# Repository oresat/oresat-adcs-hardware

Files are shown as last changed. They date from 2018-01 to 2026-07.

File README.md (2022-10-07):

# oresat-adcs-hardware

For more information on the OreSat project, please see <https://www.oresat.org/>!

## About this Repo

This repo contains the following projects:

* **The OreSat ADCS Card**
   * ADCS M0 microcontroller on its own OreSat Power Domain (OPD)
      * Power switch and LTC4300 that connects the M0 to:
         * BMI088 IMU (onboard the ADCS card)
         * LTC4305 2-Channel I2C Bus Multiplexer (one on each end cap via the backplane, end cards, and connectors to the end caps)
            * Two MMC5883MA magnetometers (two on each end cap, multiplexed by the LTC4305s)
      * Three STSPIN250s for the X, Y, and Z magnetorquers
   * Q1 Reaction Wheel OPD which powers the Q1 RW board
   * Q2 Reaction Wheel OPD which powers the Q2 RW board
   * Q3 Reaction Wheel OPD which powers the Q3 RW board
   * Q4 Reaction Wheel OPD which powers the Q4 RW board
* **OreSat RW boards**
   * Boards that run one of the four reaction wheels that we have.
   * Note that the "flat" version of the boards are for development

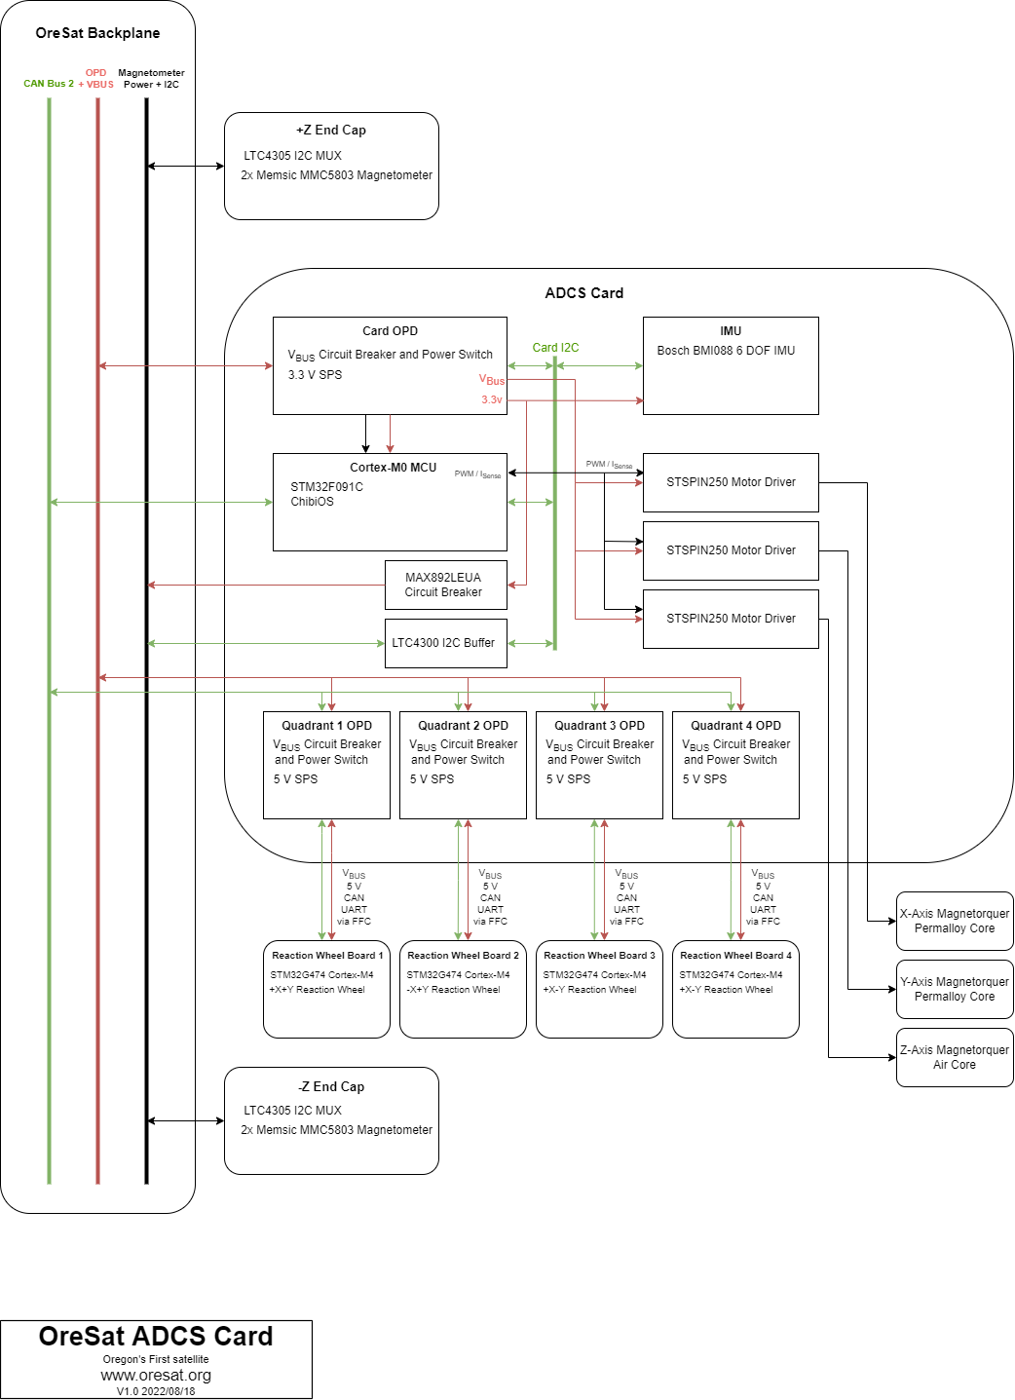
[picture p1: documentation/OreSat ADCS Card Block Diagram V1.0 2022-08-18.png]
ADCS Card Block Diagram


## LICENSE

Copyright the Portland State Aerospace Society, 2022.

This source describes Open Hardware that is licensed under CERN-OHL-S v2, or any later version.

You may redistribute and modify this source and make products using it under the terms of the CERN-OHL-S v2 (https://ohwr.org/cern_ohl_s_v2.txt).

This source is distributed WITHOUT ANY EXPRESS OR IMPLIED WARRANTY, INCLUDING OF MERCHANTABILITY, SATISFACTORY QUALITY AND FITNESS FOR A PARTICULAR PURPOSE. Please see the CERN-OHL-S v2 for applicable conditions.

Source location: https://github.com/oresat/

As per CERN-OHL-S v2 section 4, should You produce hardware based on this source, You must where practicable maintain the Source Location visible on the external case of the Gizmo or other products you make using this source.

# DEPRECATED - PLEASE EVENTUALLY REWRITE :)

## The OreSat Project
OreSat is an inter university collaboration to design an orbital vehicle. Once in orbit, the nanosatellite will engage in three missions. One of the missions is space testing a relatively new photovoltaic panel. The other missions require the ability to point at and maintain visual contact with a specified location. 
## Background Motivation   
In order to successfully complete these missions, OreSat will need to be able to articulate its orientation as well as its passive “drifting” spin (we’ll discuss what “passive spin” means a little later). 
Quick and reliable orientation adjustment and control will serve several purposes. It will allow the vehicle to direct its main camera, as well as giving it the ability to execute maneuvers that allow it to maintain visual and radio contact with a specific location. This makes taking photos and videos much easier, but it also allows us to have a segment of time to do large bandwidth data dumps to ground stations. This gives it the potential to do live video streaming. 
### Active Pointing
The method that was selected for active orientation on OreSat employs the use of internal spinning masses called reaction wheels. The basic principle is simple. If there is a free floating object and a section of it starts to spin, the rest of the body will react by spinning in the opposite direction. The spin rates are related, but not necessarily the same. If you’d like to look more into this, the concept is conservation of angular momentum. 
So the idea is that we have a pointing vector for Oresat (not poynting, that comes later), and an idea of the pointing vector to the location we would like to image. We simply take the difference, and then rotate the collective mass of all of the reaction wheels in the opposite direction until the satellite camera sees what we want it too.  
### Passive Spin Control
The term “passive spin” will be used to refer the net angular momentum of the nanosatellite. While the reaction wheels are active, they are able to control the direction and spin of the frame of the satellite, but only by effectively redistributing the momentum from the frame into the reaction wheel masses. The reaction wheels are incapable of altering the net angular momentum. The need for being able to modify the net momentum vector of the satellite helps alleviate the burden of two issues. The issues are thermal regulation and power generation. OreSat only has photovoltaic panels of its elongated faces. To maximize the amount of power, the desired passive spin of the satellite would put the long axis perpendicular to the sun. This maximizes the surface of exposure. There is another part to the total momentum though, and that is its magnitude. The rate of spin effects several things, but most notably it affects the temperature gradient experience by OreSat. If the satellite has no spin, then the side that the sun is hitting will heat continuously until OreSat passes behind the earth. This can cause several issues, most simply that having a hot spot would increase the likelihood of an electrical system to failing. Another issue is that the hot spot will cause different amounts of expansion in different areas of the frame, increasing the likelihood of failure. Another issue that hot spots cause is a drop in efficiency of the solar panels, making rotation partially an energy problem as well. 
Adding an intentional spin to OreSat will even out the thermal load applied to 

The attitude control system (ACS) inside oresat needs to orientate the position of the cubesat in space. This will be acheived in two ways; With brushless DC motors (BLDC) and with Magnetorquers. We are designing a PCB that controls both systems.

Find the project design contraints at,
[Project Design Constraints](https://github.com/oresat/oresat-acs-board/blob/master/Project%20Design%20Constraints.md)

ACS Level 2 Block Diagram Version 3.2
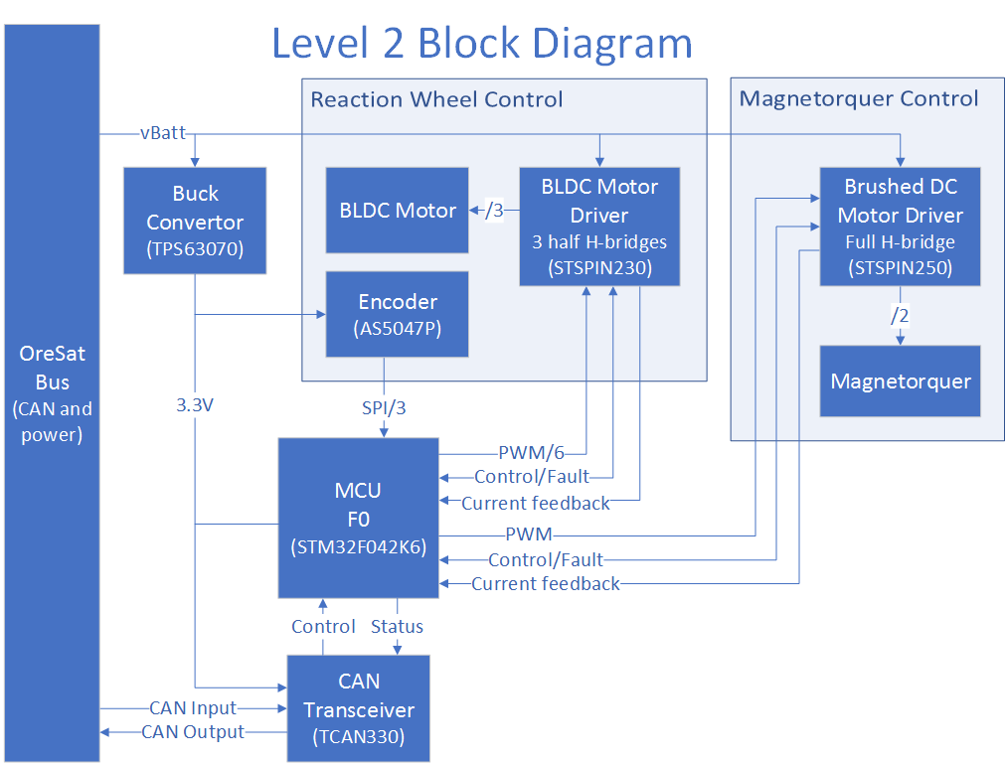
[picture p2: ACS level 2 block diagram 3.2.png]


### System Hardware Overview
[Deatailed Hardware Reference Guide](https://github.com/oresat/oresat-acs-board/tree/master/Component%20File)

### EagleCAD Files:
[Link to the EagleCAD schematics and board layouts](https://github.com/oresat/oresat-acs-board/tree/master/eaglecad)

### Manufacturing Photos:
[Manufacturing photos of board layouts and CAD model of mounting strategy](https://github.com/oresat/oresat-acs-board/tree/master/Manufacturing%20photos)

### Capstone Poster:
[Link to Capstone poster in Google Drive](https://docs.google.com/presentation/d/1KBfbX376Y7nvsIXe14JdyOgP9TMmgJlgeOiYP8BOekc/edit#slide=id.p1)
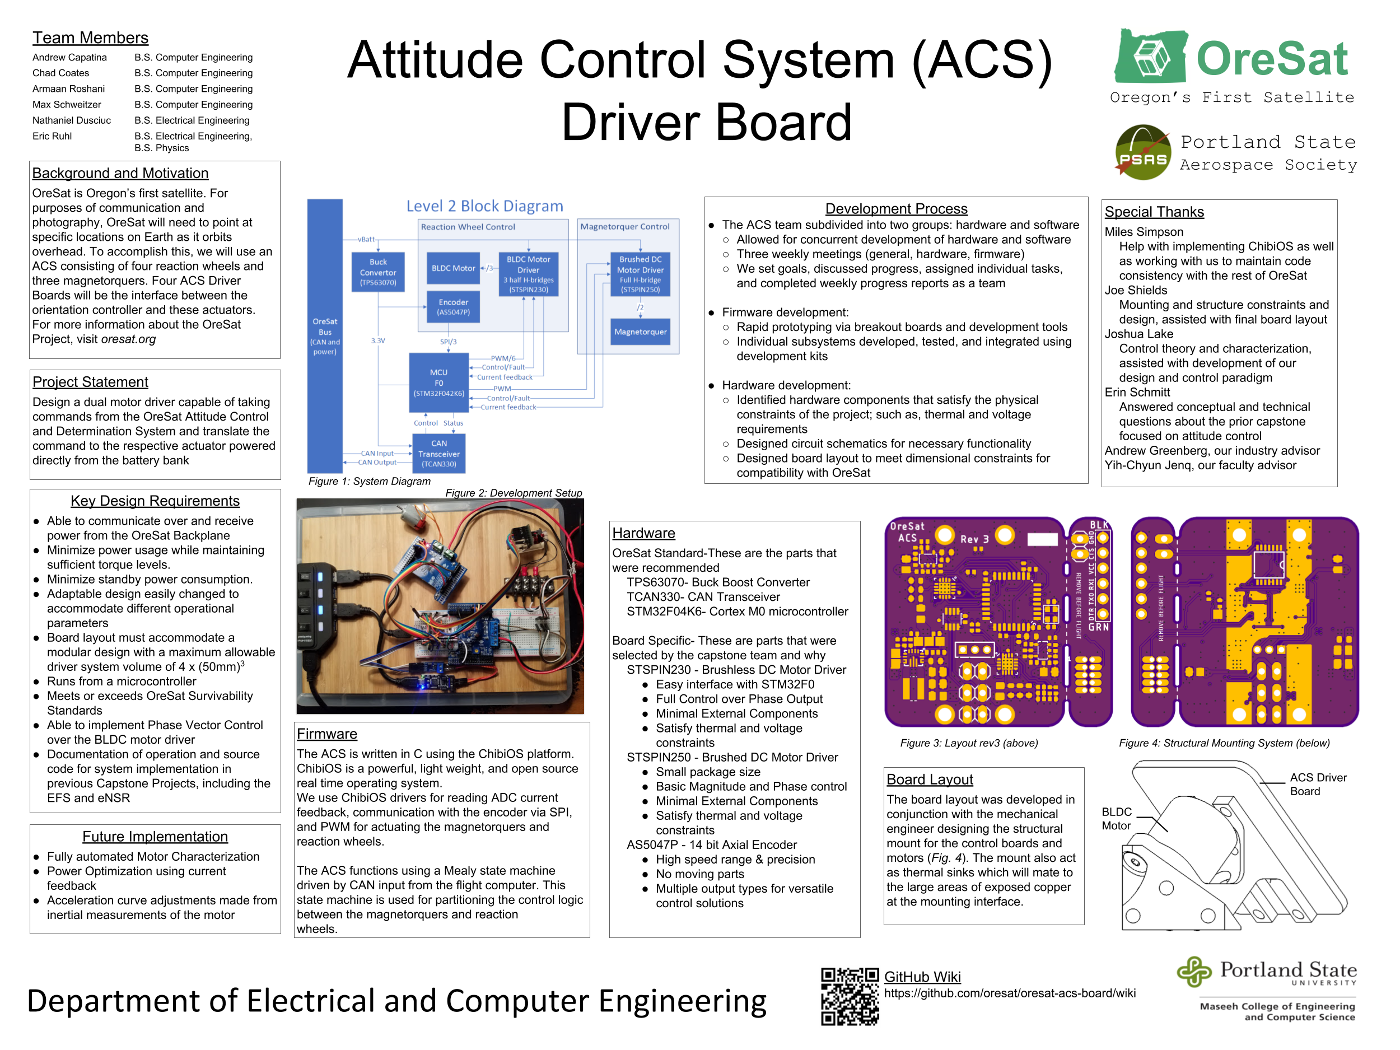
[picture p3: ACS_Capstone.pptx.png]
Image of Capstone poster


### System Firmware:
[Check here for the firmware information](https://github.com/oresat/oresat-firmware/wiki/ACS-Firmware)

### Research and Tutorials / Ramp Up Documents:
Brushless DC (BLDC) motor control is a challenging form of motor control. We found numerous helpful tutorials and references.
[Link to research references and bibliography, start here for a ramp up on ACS](https://github.com/oresat/oresat-acs-board/blob/master/Ramp%20Up.md)

## Final Product:
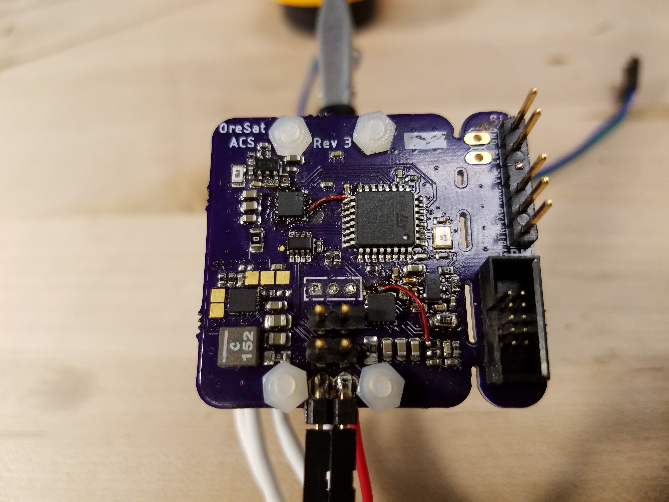
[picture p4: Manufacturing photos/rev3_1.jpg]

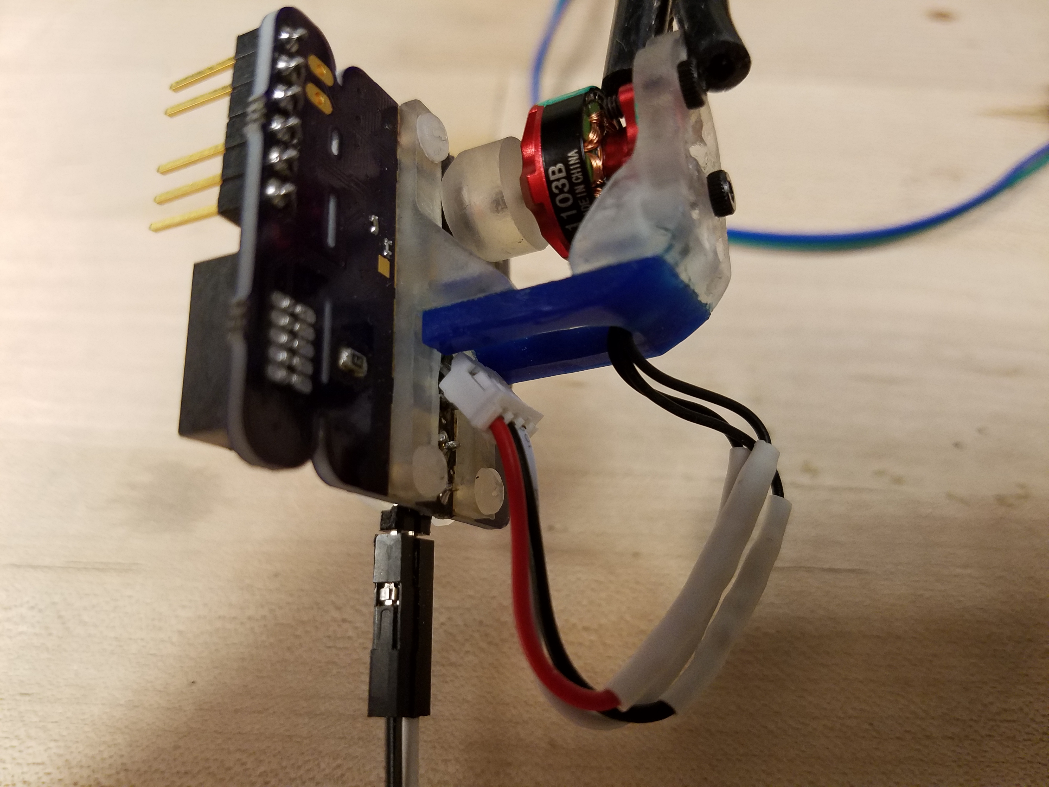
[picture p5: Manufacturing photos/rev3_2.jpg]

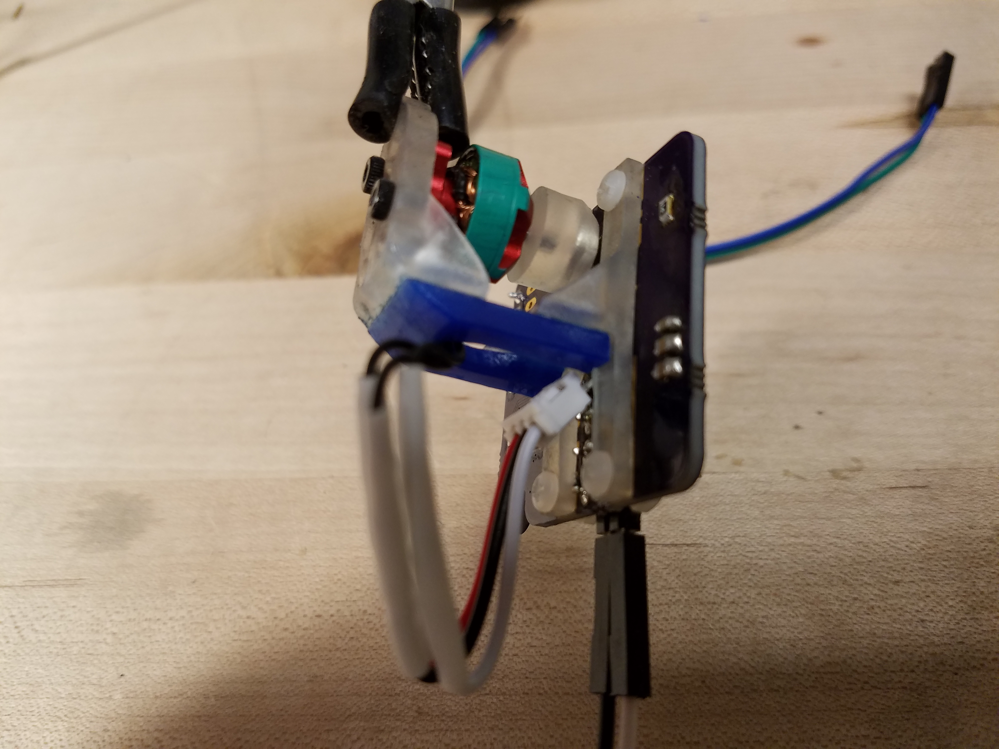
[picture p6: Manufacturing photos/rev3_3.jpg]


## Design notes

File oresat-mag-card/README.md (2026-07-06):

---
title: "**OreSat Mag Card**"
subtitle: |
  **Fabrication and Assembly Information**\
  For build TIME-STAMP
fontsize: 10pt
geometry:
  - margin=0.5in
toc: true
toc-depth: 2
colorlinks: true
urlcolor: blue
---

\newpage

# About this Board

## Board Description

The OreSat Mag Card handles three things for the open source [OreSat CubeSat system](https://www.oresat.org/):

- Reads the four magnetometers located on the end caps of the satellite and broadcasts the data on the CAN bus.
- Reads the 6 DOF inertial measurement unit (IMU) and broadcasts the data on the CAN bus (mostly just the gyroscopes).
- Runs the three magnetorquers based on commands from the C3 via the CAN bus.

## Documentation Links

- Mag card hardware Git repository: <https://github.com/oresat/oresat-adcs-hardware>
- **TODO:** Mag card Design Notes + Design Review Notes

## Documentation Files

| Filename | Notes |
| --- | --- |
| README.pdf | This README file |
| PROJECT-NAME-outline.dxf | Board outline (with holes) in DXF format |
| PROJECT-NAME-pcba.step | 3D model of PCBA (with components) |
| PROJECT-NAME-render-bot.jpg | Render of the top of the 3D model |
| PROJECT-NAME-render-bot.jpg | Render of the bottom of the 3D model |
| PROJECT-NAME-schematic.pdf | PDF of board schematics |

## Contact Information

- Website: <https://www.oresat.org/>
- Email: <oresat@pdx.edu>
- Instagram: @pdxaerospace

## Board Renders

Render of the top of the 3D model
Render of the bottom of the 3D model

\newpage

# Printed Circuit Board (PCB) Fabrication Information

## Board Info

- 4 layer board
- Bounding box is 99.8 x 94.6 mm (3.93 x 3.72 in)
- Board thickness is 1.59 mm (0.063 inch)

## Board Requirements

- Design Rules
    - Minimum Trace / Space design rules
       - Outer layers: 0.127 mm (5.0 mil) / 0.127 mm (5.0 mil)
       - Inner layers: 0.127 mm (5.0 mil) / 0.127 mm (5.0 mil)
    - Outer dimension router tolerance: +/- 0.254 mm (10.0 mil)
    - Hole placement tolerance: +/- 0.075 mm (3.0 mil)
    - Inner tab routed slot tolerance: +/- 0.254 mm (10.0 mil)
- Drills
   - Drill Positional Tolerance: 0.051 mm (2.0 mil)
   - Drill Size tolerance: +/- 0.064 mm (2.5 mil)
- Plated/Un-plated holes
  - There are 8 un-plated (NPT) holes
  - There are 730 plated through (PTH) holes
  - PTH minimum diameter: 0.254 mm (10 mil)
  - PTH minimum annulus: 0.102 mm (4 mil) radius
- Outline/Routing
  - Requires a 1.0 mm or smaller diameter routing bit
- Slots/Cutouts
  - There is one cutout.
- There are 3 fiducials on the top layer.
- Panel tabs ("mouse bites")
   - Card edges must be smooth; no mouse bites or other intrusions into the card outline.
   - If external mouse bites are required, minimize and customer will remove by hand before assembly.
- If not otherwise specified, build to IPC 6012 Class 2 or better.

## Materials

- No controlled impedance.
- Outer layers must be 1 oz Copper, inner layers can be 0.5 or 1.0 oz Copper.
- Isola FR408HR or material recommended.
- Board Surface treatment should be ENIG, althogh immersion Silver is acceptable.
- White silkscreen on top and bottom surface
- Taiyo PSR-4000 or equivalent soldermask on top and bottom, no requirements for color.

## Suggested Stack Up

| Layer | Thickness | Notes |
|---|---|---|
| Top Copper | 0.043 mm /  1.7 mil |  Layer 1 foil, 1 oz Cu after plating |
| prepreg | 0.200 mm /  7.9 mil |  Prepreg - Isola FR408HR 2113 |
| Layer 2 | 0.018 mm /  0.7 mil |  Layer 2 foil, 0.5 oz Cu |
| Core | 0.991 mm / 39 mil |  Core Isola FR408HR |
| Layer 3 | 0.018 mm /  0.7 mil |  Layer 3 foil, 0.5 oz Cu |
| prepreg | 0.200 mm /  7.9 mil |  Prepreg - Isola FR408HR 2113 |
| Bottom Copper | 0.043 mm /  1.7 mil |  Layer 4 foil, 1 oz copper after plating |
| **Total Stackup** | **1.588 mm / 62.5 mil** | |

## Array / Panel Information

- Coordinate with Contract Manufacturer (CM) for optimal size of this panel.
- If no feedback from CM, then produce single boards (no panel).

## Fabrication Files

### IPC-2581 File

| Filename | Notes |
| --- | --- |
| PROJECT-NAME-ipc2581.xml | IPC-2581 board information file |

### Legacy PCB Files

| Filename | Notes |
| ---| --- |
| PROJECT-NAME-Edge_Cuts.gbr | RS274X file for the dimension (outline) layer |
| PROJECT-NAME-F_Silkscreen.gbr | RS274X file for the top silkscreen |
| PROJECT-NAME-F_Mask.gbr | RS274X file for the top soldermask |
| PROJECT-NAME-F_Cu.gbr | RS274X file for the top copper layer |
| PROJECT-NAME-In1_Cu.gbr | RS274X file for the layer 2 copper |
| PROJECT-NAME-In2_Cu.gbr | RS274X file for the layer 3 copper |
| PROJECT-NAME-B_Cu.gbr | RS274X file for the bottom copper layer |
| PROJECT-NAME-B_Mask.gbr | RS274X file for the bottom soldermask |
| PROJECT-NAME-B_Silkscreen.gbr | RS274X file for the bottom silkscreen |
| PROJECT-NAME-NPTH.drl | Excellon file for non-plated through holes |
| PROJECT-NAME-PTH.drl | Excellon file for plated through holes | 

\newpage

# Printed Circuit Board Assembly (PCBA) Information

## Assembly Info

- This PCBA is surface mount (SMT) components with 4 through-hole (TH) components.
- Components are only on the top side of the board.

## Assembly Requirements

- Assemble to IPC Class 2 or better
- Bake components that are not moisture sealed to appropriate levels as required.
- Solder paste MUST be leaded.
- Aqueous flux and wash strongly preferred.
   - Clean to NASA Standard "Visibly Clean (VC)": No particles or residues are visible to the naked eye.
- No conformal coating.
- Ship in antistatic protective bag

## Component Specific Assembly Information

- No specific requirements.

## Assembly Files

### IPC-2581 File

| Filename | Notes |
| --- | --- |
| PROJECT-NAME-ipc2581.xml | IPC-2581 board information file |

### Bill of Materials (BOM)

| Filename | Description |
| --- | --- |
| PROJECT-NAME-bom.csv | BOM in Comma Separated Variable format |

### Solder Paste Stencils

| Filename | Notes |
| --- | --- |
| PROJECT-NAME-B_Paste.gbr | RS274X file for top/front solder paste stencil |
| PROJECT-NAME-F_Paste.gbr | RS274X file for bottom/back solder paste stencil |

### Mounting/Placement Location

| Filename | Description |
| --- | --- |
| PROJECT-NAME-3u.pos | Pick and place locations for components |

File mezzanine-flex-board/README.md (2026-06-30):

---
title: "**OreSat Reaction Wheel Flex Board**"
subtitle: |
  **Fabrication and Assembly Information**\
  For build TIME-STAMP
fontsize: 10pt
geometry:
  - margin=0.5in
toc: true
toc-depth: 2
colorlinks: true
urlcolor: blue
---

\newpage

# About this Board

## Board Description

This flexible circuit board connects the OreSat Reaction Wheel boards (the boards that control each reaction wheel) to the
the OreSat RW Card, which handles the OreSat Power Domain for each RW. For more information, see the open source 
[OreSat CubeSat system](https://www.oresat.org/)

## Documentation Links

- Git repository: <https://github.com/oresat/oresat-adcs-hardware>
- **TODO:** Link to Design Notes + Design Review Notes

## Documentation Files

| Filename | Notes |
| --- | --- |
| README.pdf | This README file |
| PROJECT-NAME-outline.dxf | Board outline (with holes) in DXF format |
| PROJECT-NAME-pcba.step | 3D model of PCBA (with components) |
| PROJECT-NAME-render-bot.jpg | Render of the top of the 3D model |
| PROJECT-NAME-render-bot.jpg | Render of the bottom of the 3D model |
| PROJECT-NAME-schematic.pdf | PDF of board schematics |

## Contact Information

- Website: <https://www.oresat.org/>
- Email: <oresat@pdx.edu>
- Instagram: @pdxaerospace

## Board Renders

Render of the top of the 3D model
Render of the bottom of the 3D model

Note that renders do not show stiffeners.

\newpage

# Printed Circuit Board (PCB) Fabrication Information

## Board Info

- 2 layer board
- Bounding box is 39.5 x 10.2 mm
- Flexible PCB with two polimide stiffeners (see below)
- Note that these boards were originally run and tested using JLCPCB's flexible PCB service.

## Board Requirements

- Design Rules
    - Minimum Trace / Space design rules
       - Outer layers: 0.127 mm (5.0 mil) / 0.127 mm (5.0 mil)
       - Inner layers: 0.127 mm (5.0 mil) / 0.127 mm (5.0 mil)
    - Outer dimension router tolerance: +/- 0.254 mm (10.0 mil)
    - Hole placement tolerance: +/- 0.075 mm (3.0 mil)
    - Inner tab routed slot tolerance: +/- 0.254 mm (10.0 mil)
- Drills
   - Drill Positional Tolerance: 0.051 mm (2.0 mil)
   - Drill Size tolerance: +/- 0.064 mm (2.5 mil)
- Plated/Un-plated holes
  - PTH minimum diameter: 0.3 mm (11.8 mil)
  - PTH minimum annulus: 0.2 mm (7.9 mil)
- Outline/Routing
  - No requirements
- Slots
  - There are no slots.
- Cutouts
  - There are no cutouts.
- There are no fiducials.
- Panel tabs ("mouse bites")
   - No requirements; prefer that board edges are smooth; no mouse bites or other intrusions into the card outline.
   - If external mouse bites are required, minimize and customer will remove by hand before assembly.
- If not otherwise specified, build to IPC 6012 Class 2 or better.

## Materials

- No controlled impedance.
- Note that these boards were originally run and tested using JLCPCB's flexible PCB service, and so numbers here are arbitrarily from that service. Other thicknesses can be used, contact us to discuss.
- 0.33 to 0.5 oz Copper.
- Polyimide flexible circuit material, 25 um thick dielectric
- Coverlay (soldermask equivalent) is 12.5 um Polyimide
- There are two 0.25 mm thick Polyimide stiffeners on the TOP surface, one on each end.
   - These can be FR4 stiffeners if easier / cheaper. 
- Board Surface treatment should be ENIG.
- White silkscreen on top and bottom surface

## Suggested Stack Up

| Layer | Thickness | Notes |
|---|---|---|
| Top Stiffener | 0.25 mm  / 9.84 mils | Stiffener on top surface of board only |
| Top Coverlay | 12.5 um /  0.49 mils | Coverlay / Solder mask |
| Top Copper | 18.0 um /  0.71 mils | Layer 1 foil, 0.5 oz Cu after plating  |
| Polyimide Core  | 25.0 um /  0.98 mils | Polyimide flex material |
| Bottom Copper | 18.0 um /  0.71 mils | Layer 2 foil, 0.5 oz Cu after plating  |
| Bottom Coverlay | 12.5 um /  0.49 mils | Coverlay / Solder mask |

Total thickness: 86 um (without stiffener)

## Array / Panel Information

- No panel or array required.

## Fabrication Files

### IPC-2581 File

| Filename | Notes |
| --- | --- |
| PROJECT-NAME-ipc2581.xml | IPC-2581 board information file |

### Legacy PCB Files

| Filename | Notes |
| --- | --- |
| PROJECT-NAME-Edge_Cuts.gbr | RS274X file for the dimension (outline) layer |
| PROJECT-NAME-F_Silkscreen.gbr | RS274X file for the top silkscreen |
| PROJECT-NAME-F_Mask.gbr | RS274X file for the top soldermask |
| PROJECT-NAME-F_Cu.gbr | RS274X file for the top copper layer |
| PROJECT-NAME-B_Cu.gbr | RS274X file for the bottom copper layer |
| PROJECT-NAME-B_Mask.gbr | RS274X file for the bottom soldermask |
| PROJECT-NAME-B_Silkscreen.gbr | RS274X file for the bottom silkscreen |
| PROJECT-NAME-User_Stiffeners.gbr | RS274X file for PI stiffener | 
| PROJECT-NAME-PTH.drl | Excellon file for plated through holes | 

\newpage

# Printed Circuit Board Assembly (PCBA) Information

## Assembly Info

- There are SMT components only on the bottom side of the board.

## Assembly Requirements

- Assemble to IPC Class 2 or better
- Bake components that are not moisture sealed to appropriate levels as required.
- Solder paste MUST be leaded.
- Aqueous flux and wash strongly preferred.
   - Clean to NASA Standard "Visibly Clean (VC)": No particles or residues are visible to the naked eye.
- No conformal coating.

## Component Specific Assembly Information

- No specific requirements.

## Assembly Files

### IPC-2581 File

| Filename | Notes |
| --- | --- |
| PROJECT-NAME-ipc2581.xml | IPC-2581 board information file |

### Bill of Materials (BOM)

| Filename | Description |
| --- | --- |
| PROJECT-NAME-bom.csv | BOM in Comma Separated Variable format |

### Solder Paste Stencils

| Filename | Notes |
| --- | --- |
| PROJECT-NAME-B_Paste.gbr | RS274X file for top/front solder paste stencil |
| PROJECT-NAME-F_Paste.gbr | RS274X file for bottom/back solder paste stencil |

### Mounting/Placement Location

| Filename | Description |
| --- | --- |
| PROJECT-NAME-3u.pos | Pick and place locations for components |

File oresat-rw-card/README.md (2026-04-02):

---
title: "**OreSat Reaction Wheel (RW) Card**"
subtitle: |
  **Fabrication and Assembly Information**\
  For build TIME-STAMP
fontsize: 10pt
geometry:
  - margin=0.5in
toc: true
toc-depth: 2
colorlinks: true
urlcolor: blue
---

\newpage

# About this Board

## Board Description

The OreSat RW Card run the four reaction wheels on the open source [OreSat CubeSat system](https://www.oresat.org/). The RW card:

- Has an OreSat Power Domain (OPD) per reaction wheel.
- Requires a flexible cable between the card and the RW board.

## Documentation Links

- RW card hardware Git repository: <https://github.com/oresat/oresat-adcs-hardware>
- **TODO:** RW card Design Notes + Design Review Notes

## Documentation Files

| Filename | Notes |
| --- | --- |
| README.pdf | This README file |
| PROJECT-NAME-outline.dxf | Board outline (with holes) in DXF format |
| PROJECT-NAME-pcba.step | 3D model of PCBA (with components) |
| PROJECT-NAME-render-bot.jpg | Render of the top of the 3D model |
| PROJECT-NAME-render-bot.jpg | Render of the bottom of the 3D model |
| PROJECT-NAME-schematic.pdf | PDF of board schematics |

## Contact Information

- Website: <https://www.oresat.org/>
- Email: <oresat@pdx.edu>
- Instagram: @pdxaerospace

## Board Renders

Render of the top of the 3D model
Render of the bottom of the 3D model

\newpage

# Printed Circuit Board (PCB) Fabrication Information

## Board Info

- 4 layer board
- Bounding box is 99.8 x 94.6 mm (3.93 x 3.72 in)
- Board thickness is 1.59 mm (0.063 inch)

## Board Requirements

- Design Rules
    - Minimum Trace / Space design rules
       - Outer layers: 0.127 mm (5.0 mil) / 0.127 mm (5.0 mil)
       - Inner layers: 0.127 mm (5.0 mil) / 0.127 mm (5.0 mil)
    - Outer dimension router tolerance: +/- 0.254 mm (10.0 mil)
    - Hole placement tolerance: +/- 0.075 mm (3.0 mil)
    - Inner tab routed slot tolerance: +/- 0.254 mm (10.0 mil)
- Drills
   - Drill Positional Tolerance: 0.051 mm (2.0 mil)
   - Drill Size tolerance: +/- 0.064 mm (2.5 mil)
- Plated/Un-plated holes
  - There are 2 un-plated (NPT) holes
  - There are 664 plated through (PTH) holes
  - PTH minimum diameter: 0.254 mm (10 mil)
  - PTH minimum annulus: 0.102 mm (4 mil) radius
- Outline/Routing
  - Requires a 1.0 mm or smaller diameter routing bit
- Slots
  - There is one cutout.
- Cutouts
  - There are no cutouts
- There are 3 fiducials on the top layer and 3 fiducials on the bottom layer.
- Panel tabs ("mouse bites")
   - Card edges must be smooth; no mouse bites or other intrusions into the card outline.
   - If external mouse bites are required, minimize and customer will remove by hand before assembly.
- If not otherwise specified, build to IPC 6012 Class 2 or better.

## Materials

- No controlled impedance.
- Outer layers must be 1 oz Copper, inner layers can be 0.5 or 1.0 oz Copper.
- Isola FR408HR or material recommended.
- Board Surface treatment should be ENIG, althogh immersion Silver is acceptable.
- White silkscreen on top and bottom surface
- Taiyo PSR-4000 or equivalent soldermask on top and bottom, no requirements for color.

## Suggested Stack Up

| Layer | Thickness | Notes |
|---|---|---|
| Top Copper | 0.043 mm /  1.7 mil |  Layer 1 foil, 1 oz Cu after plating |
| prepreg | 0.200 mm /  7.9 mil |  Prepreg - Isola FR408HR 2113 |
| Layer 2 | 0.018 mm /  0.7 mil |  Layer 2 foil, 0.5 oz Cu |
| Core | 0.991 mm / 39 mil |  Core Isola FR408HR |
| Layer 3 | 0.018 mm /  0.7 mil |  Layer 3 foil, 0.5 oz Cu |
| prepreg | 0.200 mm /  7.9 mil |  Prepreg - Isola FR408HR 2113 |
| Bottom Copper | 0.043 mm /  1.7 mil |  Layer 4 foil, 1 oz copper after plating |
| **Total Stackup** | **1.588 mm / 62.5 mil** | |

## Array / Panel Information

- Coordinate with Contract Manufacturer (CM) for optimal size of this panel.
- If no feedback from CM, then produce single boards (no panel).

## Fabrication Files

### IPC-2581 File

| Filename | Notes |
| --- | --- |
| PROJECT-NAME-ipc2581.xml | IPC-2581 board information file |

### Legacy PCB Files

| Filename | Notes |
| ---| --- |
| PROJECT-NAME-Edge_Cuts.gbr | RS274X file for the dimension (outline) layer |
| PROJECT-NAME-F_Silkscreen.gbr | RS274X file for the top silkscreen |
| PROJECT-NAME-F_Mask.gbr | RS274X file for the top soldermask |
| PROJECT-NAME-F_Cu.gbr | RS274X file for the top copper layer |
| PROJECT-NAME-In1_Cu.gbr | RS274X file for the layer 2 copper |
| PROJECT-NAME-In2_Cu.gbr | RS274X file for the layer 3 copper |
| PROJECT-NAME-B_Cu.gbr | RS274X file for the bottom copper layer |
| PROJECT-NAME-B_Mask.gbr | RS274X file for the bottom soldermask |
| PROJECT-NAME-B_Silkscreen.gbr | RS274X file for the bottom silkscreen |
| PROJECT-NAME-NPTH.drl | Excellon file for non-plated through holes |
| PROJECT-NAME-PTH.drl | Excellon file for plated through holes | 

\newpage

# Printed Circuit Board Assembly (PCBA) Information

## Assembly Info

- There are components on the top and bottom sides of the board.
- This PCBA is mostly surface mount (SMT) with a one through-hole (THT) components.

## Assembly Requirements

- Assemble to IPC Class 2 or better
- Bake components that are not moisture sealed to appropriate levels as required.
- Solder paste MUST be leaded.
- Aqueous flux and wash strongly preferred.
   - Clean to NASA Standard "Visibly Clean (VC)": No particles or residues are visible to the naked eye.
- No conformal coating.
- Ship in antistatic protective bag

## Component Specific Assembly Information

- No specific requirements.

## Assembly Files

### IPC-2581 File

| Filename | Notes |
| --- | --- |
| PROJECT-NAME-ipc2581.xml | IPC-2581 board information file |

### Bill of Materials (BOM)

| Filename | Description |
| --- | --- |
| PROJECT-NAME-bom.csv | BOM in Comma Separated Variable format |

### Solder Paste Stencils

| Filename | Notes |
| --- | --- |
| PROJECT-NAME-B_Paste.gbr | RS274X file for top/front solder paste stencil |
| PROJECT-NAME-F_Paste.gbr | RS274X file for bottom/back solder paste stencil |

### Mounting/Placement Location

| Filename | Description |
| --- | --- |
| PROJECT-NAME-3u.pos | Pick and place locations for components |

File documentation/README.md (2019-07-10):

# Introduction
## The OreSat Project
OreSat is an inter university collaboration to design an orbital vehicle. Once in orbit, the nanosatellite will engage in three missions. One of the missions is space testing a relatively new photovoltaic panel. The other missions require the ability to point at and maintain visual contact with a specified location as the cube sat passes over it. 
## Background Motivation
In order to successfully complete these missions, OreSat will need to be able to articulate its orientation as well as its passive “drifting” spin (we’ll discuss what “passive spin” means a little later). 
Quick and reliable orientation adjustment and control will serve several purposes. It will allow the vehicle to direct its main camera, as well as giving it the ability to execute maneuvers that allow it to maintain visual and radio contact with a specific location. This makes taking photos and videos much easier, but it also allows us to have a segment of time to do large bandwidth data dumps to ground stations. This gives it the potential to do live video streaming. 
### Active Pointing
The method that was selected for active orientation on OreSat employs the use of internal spinning masses called reaction wheels. The basic principle is simple. If there is a free floating object and a section of it starts to spin, the rest of the body will react by spinning in the opposite direction. The spin rates are related, but not necessarily the same. If you’d like to look more into this, the concept is conservation of angular momentum. 
So the idea is that we have a pointing vector for Oresat (not poynting, that comes later), and an idea of the pointing vector to the location we would like to image. We simply take the difference, and then rotate the collective mass of all of the reaction wheels in the opposite direction until the satellite camera sees what we want it too.  
### Passive Spin Control
The term “passive spin” will be used to refer the net angular momentum of the nanosatellite. While the reaction wheels are active, they are able to control the direction and spin of the frame of the satellite, but only by effectively redistributing the momentum from the frame into the reaction wheel masses. The reaction wheels are incapable of altering the net angular momentum. The need for being able to modify the net momentum vector of the satellite helps alleviate the burden of two issues. The issues are thermal regulation and power generation. OreSat only has photovoltaic panels of its elongated faces. To maximize the amount of power, the desired passive spin of the satellite would put the long axis perpendicular to the sun. This maximizes the surface of exposure. There is another part to the total momentum though, and that is its magnitude. The rate of spin effects several things, but most notably it affects the temperature gradient experience by OreSat. If the satellite has no spin, then the side that the sun is hitting will heat continuously until OreSat passes behind the earth. This can cause several issues, most simply that having a hot spot would increase the likelihood of an electrical system to failing. Another issue is that the hot spot will cause different amounts of expansion in different areas of the frame, increasing the likelihood of failure. Another issue that hot spots cause is a drop in efficiency of the solar panels, making rotation partially an energy problem as well. 
Adding an intentional spin to OreSat will even out the thermal load applied to 

The attitude control system (ACS) inside oresat needs to orientate the position of the cubesat in space. This will be acheived in two ways; With brushless DC motors (BLDC) and with Magnetorquers. We are designing a PCB that controls both systems.

# Reference Links for Motor Control:

[ESC on Wikipedia](https://en.wikipedia.org/wiki/Electronic_speed_control)<br/>
This is a basic overview of electronic speed controlers

[BLDC control with an ESC](https://os.mbed.com/users/4180_1/notebook/using-a-dc-brushless-motor-with-an-rc-esc/)<br/>
The 'Hello World' of ESC demos

[VESC github](https://github.com/vedderb/bldc)<br/>
Ha ha... Good luck.

[VESC – open source ESC](http://vedder.se/2015/01/vesc-open-source-esc/)<br/>
How to navigate the vedderb github page

[BLDC motor control tutorial (part 1)](https://www.youtube.com/watch?v=ZAY5JInyHXY)

[BLDC motor control tutorial (part 2)](https://www.youtube.com/watch?v=WyQInXjpGwU)

[Sinusoidal control](https://www.digikey.com/en/articles/techzone/2017/jan/why-and-how-to-sinusoidally-control-three-phase-brushless-dc-motors)<br/>
This is an introduction to how sinusoidal wave forms are used for phase vector control

[Intro to Instaspin](https://www.youtube.com/watch?v=szgVUfyX8JM)<br/>
This is a solid explination for how motor control signals move a motor as well as what back emf is and how it is implemented

[ACS design for cubesats – research article](https://www.hindawi.com/journals/jcse/2013/657182/)

[Anti-cogging control](https://hackaday.com/2016/02/23/anti-cogging-algorithm-brings-out-the-best-in-your-hobby-brushless-motors/)

[Implementing Embedded Speed Control For Brushless DC Motors](https://www.embedded.com/design/real-time-and-performance/4006783/Implementing-Embedded-Speed-Control-for-Brushless-DC-Motors-Part-4)

# Bibliography in APA format:

Electronic speed control. Retrieved from https://en.wikipedia.org/wiki/Electronic_speed_control
 
Jim Hamblen, (05/13/2017). Using a Brushless DC motor with an RC ESC. Retrieved from     
    https://os.mbed.com/users/4180_1/notebook/using-a-dc-brushless-motor-with-an-rc-esc/
	
Benjamin Vedder, (01/07/2015). VESC - Open Source ESC. Retrieved from
    http://vedder.se/2015/01/vesc-open-source-esc/
	
Benjamin Vedder, (01/07/2015). VESC GitHub. Retrieved from
    https://github.com/vedderb/bldc
	
Texas Instruments, (06/11/2012). Brushless DC Motors & Control - How it Works (Part 1 of 2).
    Retrieved from https://www.youtube.com/watch?v=ZAY5JInyHXY 
	
Texas Instruments, (06/11/2012). Brushless DC Motors & Control - How it Works (Part 2 of 2).
    Retrieved from https://www.youtube.com/watch?v=WyQInXjpGwU 
	
Digikey editors, (01/17/2017). Why and How to Sinusoidally Control Three-Phase Brushless DC 
    Motors. Retrieved from 
https://www.digikey.com/en/articles/techzone/2017/jan/why-and-how-to-sinusoidally-control-three-phase-brushless-dc-motors

Texas Instruments, (02/13/2012). Introduction to InstaSPIN™-BLDC Motor Control Solution.
Retrieved from https://www.youtube.com/watch?v=szgVUfyX8JM 

Junquan Li, Mark Post, Thomas Wright, and Regina Lee, (12/18/2012). Design of Attitude
    Control Systems for CubeSat-Class Nanosatellite. Retrieved from
    https://www.hindawi.com/journals/jcse/2013/657182/ 
	
Joshua Vasquez, (02/23/2016). Anti-Cogging Algorithm Brings Out the Best in your Hobby 
    Brushless Motors. Retrieved from
https://hackaday.com/2016/02/23/anti-cogging-algorithm-brings-out-the-best-in-your-hobby-brushless-motors/

Yashvant Jani, (01/15/2017). Implementing Embedded Speed Control for Brushless DC Motors. Retrieved from 
https://www.embedded.com/design/real-time-and-performance/4006783/Implementing-Embedded-Speed-Control-for-Brushless-DC-Motors-Part-4

# Bibliography in IEEE format:

En.wikipedia.org. (2018). Electronic speed control. [online] Available at: https://en.wikipedia.org/wiki/Electronic_speed_control [Accessed 22 May 2018].

Hamblen, J. (2018). Using a Brushless DC motor with an RC ESC | Mbed. [online] Os.mbed.com. Available at: https://os.mbed.com/users/4180_1/notebook/using-a-dc-brushless-motor-with-an-rc-esc/ [Accessed 22 May 2018].

Vedder, B. (2018). VESC – Open Source ESC | Benjamin's robotics. [online] Vedder.se. Available at: http://vedder.se/2015/01/vesc-open-source-esc/ [Accessed 22 May 2018].

Vedder, B. (2018). vedderb/bldc. [online] GitHub. Available at: https://github.com/vedderb/bldc [Accessed 22 May 2018].

Texas Instruments, YouTube. (2018). Brushless DC Motors & Control - How it Works (Part 1 of 2). [online] Available at: https://www.youtube.com/watch?v=ZAY5JInyHXY [Accessed 22 May 2018].

Texas Instruments, YouTube. (2018). Brushless DC Motors & Control - How it Works (Part 2 of 2). [online] Available at: https://www.youtube.com/watch?v=WyQInXjpGwU [Accessed 22 May 2018].

Digikey.com. (2018). Why and How to Control Brushless DC Motors | DigiKey. [online] Available at: https://www.digikey.com/en/articles/techzone/2017/jan/why-and-how-to-sinusoidally-control-three-phase-brushless-dc-motors [Accessed 22 May 2018].

Texas Instruments, En.wikipedia.org. (2018). Electronic speed control. [online] Available at: https://en.wikipedia.org/wiki/Electronic_speed_control [Accessed 22 May 2018].

Junquan Li, Mark Post, Thomas Wright, and Regina Lee. Design of Attitude Control Systems for CubeSat-Class Nanosatellite [online]. Journal of Control Science and Engineering, vol. 2013, Article ID 657182, 15 pages, 2013. Available at: https://www.hindawi.com/journals/jcse/2013/657182/cta/

Vasquez, J. (2018). Anti-Cogging Algorithm Brings Out the Best in your Hobby Brushless Motors. [online] Hackaday. Available at: https://hackaday.com/2016/02/23/anti-cogging-algorithm-brings-out-the-best-in-your-hobby-brushless-motors/ [Accessed 22 May 2018].

Yashvant Jani, (2017). Implementing Embedded Speed Control for Brushless DC Motors. [online] embedded. Available at:
https://www.embedded.com/design/real-time-and-performance/4006783/Implementing-Embedded-Speed-Control-for-Brushless-DC-Motors-Part-4 [Accessed 22 May 2018].

Chibi OS: SPI Driver. (n.d.) [online] Available at:
    http://chibios.sourceforge.net/html/group___s_p_i.html

Chibi OS: PWM Driver. (n.d.) [online] Available at:
    http://chibios.sourceforge.net/html/group___p_w_m.html

Chibi OS: ADC Driver. (n.d.) [online] Available at:
    http://chibios.sourceforge.net/html/group___a_d_c.html

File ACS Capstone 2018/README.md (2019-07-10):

# OreSat ACS Driver Board

# Introduction
## The OreSat Project
OreSat is an inter university collaboration to design an orbital vehicle. Once in orbit, the nanosatellite will engage in three missions. One of the missions is space testing a relatively new photovoltaic panel. The other missions require the ability to point at and maintain visual contact with a specified location. 
## Background Motivation   
In order to successfully complete these missions, OreSat will need to be able to articulate its orientation as well as its passive “drifting” spin (we’ll discuss what “passive spin” means a little later). 
Quick and reliable orientation adjustment and control will serve several purposes. It will allow the vehicle to direct its main camera, as well as giving it the ability to execute maneuvers that allow it to maintain visual and radio contact with a specific location. This makes taking photos and videos much easier, but it also allows us to have a segment of time to do large bandwidth data dumps to ground stations. This gives it the potential to do live video streaming. 
### Active Pointing
The method that was selected for active orientation on OreSat employs the use of internal spinning masses called reaction wheels. The basic principle is simple. If there is a free floating object and a section of it starts to spin, the rest of the body will react by spinning in the opposite direction. The spin rates are related, but not necessarily the same. If you’d like to look more into this, the concept is conservation of angular momentum. 
So the idea is that we have a pointing vector for Oresat (not poynting, that comes later), and an idea of the pointing vector to the location we would like to image. We simply take the difference, and then rotate the collective mass of all of the reaction wheels in the opposite direction until the satellite camera sees what we want it too.  
### Passive Spin Control
The term “passive spin” will be used to refer the net angular momentum of the nanosatellite. While the reaction wheels are active, they are able to control the direction and spin of the frame of the satellite, but only by effectively redistributing the momentum from the frame into the reaction wheel masses. The reaction wheels are incapable of altering the net angular momentum. The need for being able to modify the net momentum vector of the satellite helps alleviate the burden of two issues. The issues are thermal regulation and power generation. OreSat only has photovoltaic panels of its elongated faces. To maximize the amount of power, the desired passive spin of the satellite would put the long axis perpendicular to the sun. This maximizes the surface of exposure. There is another part to the total momentum though, and that is its magnitude. The rate of spin effects several things, but most notably it affects the temperature gradient experience by OreSat. If the satellite has no spin, then the side that the sun is hitting will heat continuously until OreSat passes behind the earth. This can cause several issues, most simply that having a hot spot would increase the likelihood of an electrical system to failing. Another issue is that the hot spot will cause different amounts of expansion in different areas of the frame, increasing the likelihood of failure. Another issue that hot spots cause is a drop in efficiency of the solar panels, making rotation partially an energy problem as well. 
Adding an intentional spin to OreSat will even out the thermal load applied to 

The attitude control system (ACS) inside oresat needs to orientate the position of the cubesat in space. This will be acheived in two ways; With brushless DC motors (BLDC) and with Magnetorquers. We are designing a PCB that controls both systems.

# Project Overview
## Block Diagram
ACS Level 2 Block Diagram Version 3.2


| **System Block** | **Hardware Chosen and Reasons Why** |
| :--- | :--- |
| Buck Converter | TPS63070 <br/>We chose this part because of oresat heritage. This component is being used elsewhere in oresat and we were recommended to use it. It is a buck-boost converter that can take a wide range of input voltage. Overall, it is a robust component. |
| BLDC Motor | What motor??? |
| BLDC Motor Driver | STSPIN 230 <br/>We chose this component for a number of reasons. Namely;  <br/> - Satisfies thermal and voltage constraints. <br/> - Small form-factor. <br/> - Half-H-Bridge control over each phase of the BLDC. <br/> - Easy interface with STM32F0. <br/> - Full Control over Phase Output. <br/> - Minimal External Components. | 
| Encoder | AS5047P <br/>The AS5047P utilizes an array of Hall effect sensors and a diametric magnet to provide a precise position reading. The sensor provides sufficient precision and provides output data in multiple convenient forms. See the datasheet for details. |
| MCU F0 | STM32F042K6 <br/>We chose this MCU because of oresat heritage. It is being used elsewhere in oresat. This MCU has a small form factor and is power efficient. | 
| CAN Transceiver | TCAN330 <br/>We were told to use this component because of oresat design heritage. The rest of oresat is using this CAN transceiver. |
| Brushed DC Motor Driver | STSPIN250 <br/> We chose this component for a number of reasons. Namely: <br/> - Satisfy thermal and voltage constraints <br/> - Small package size <br/> - Full H-Bridge control <br/> - Basic Magnitude and Phase control <br/> - Minimal External Components | 
| Magnetorquer | Still to be determined. <br/> The magnetorquer will essentially be an inductor most likely in a flat spiral orientation to save volume inside oresat. |

## Schematic
Rev1.1:
* The “flatsat” version that we manufactured and tested.
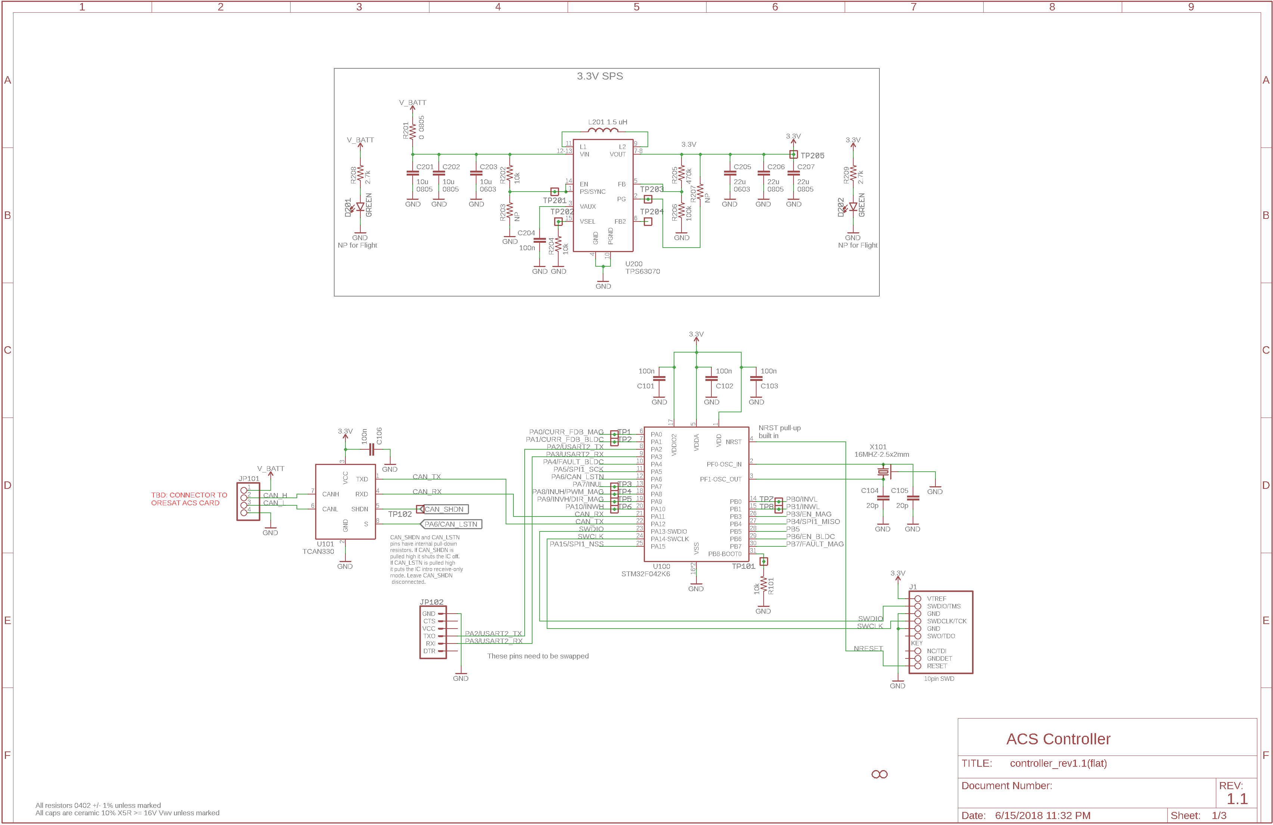
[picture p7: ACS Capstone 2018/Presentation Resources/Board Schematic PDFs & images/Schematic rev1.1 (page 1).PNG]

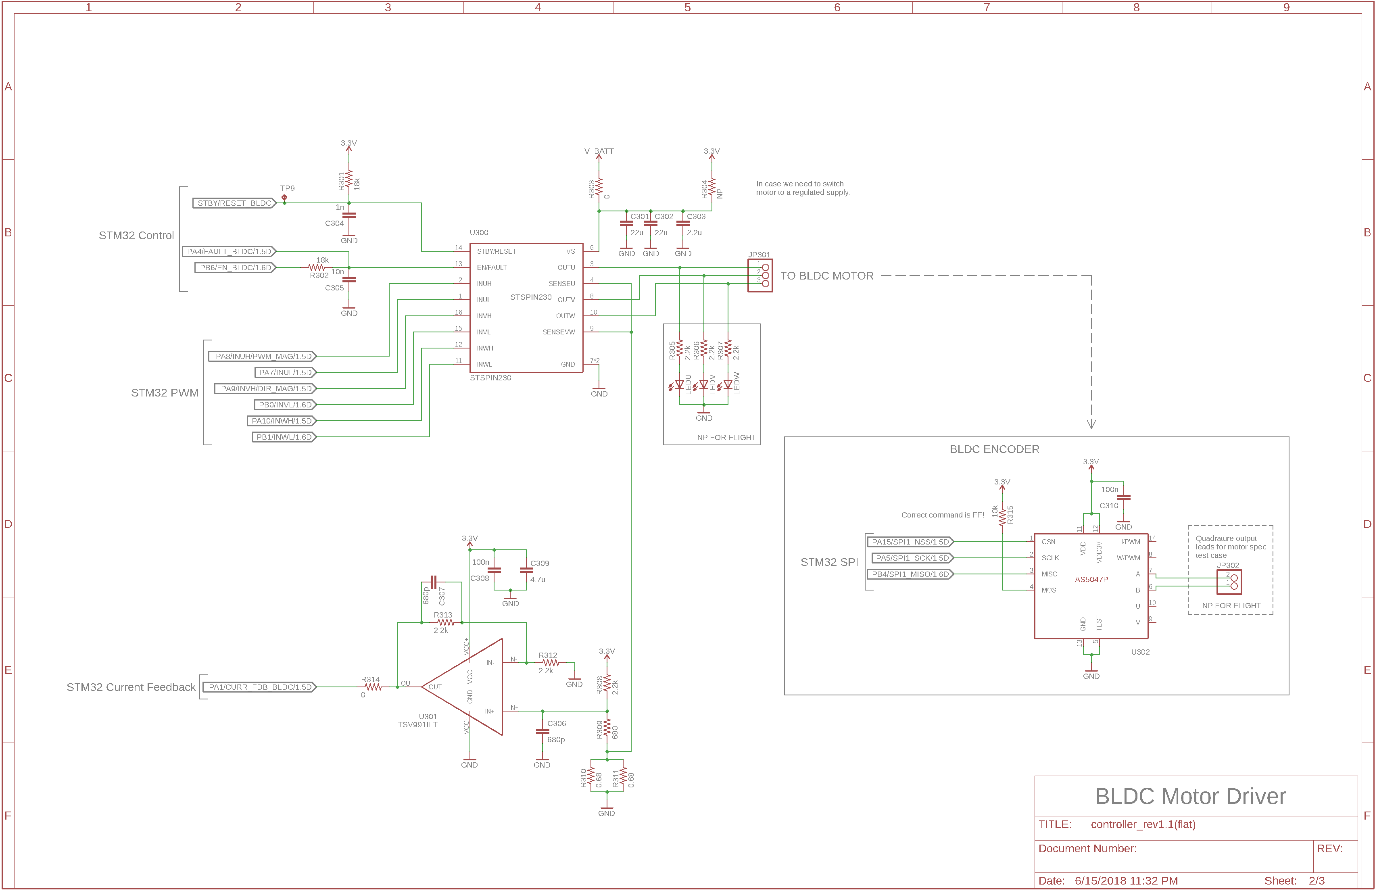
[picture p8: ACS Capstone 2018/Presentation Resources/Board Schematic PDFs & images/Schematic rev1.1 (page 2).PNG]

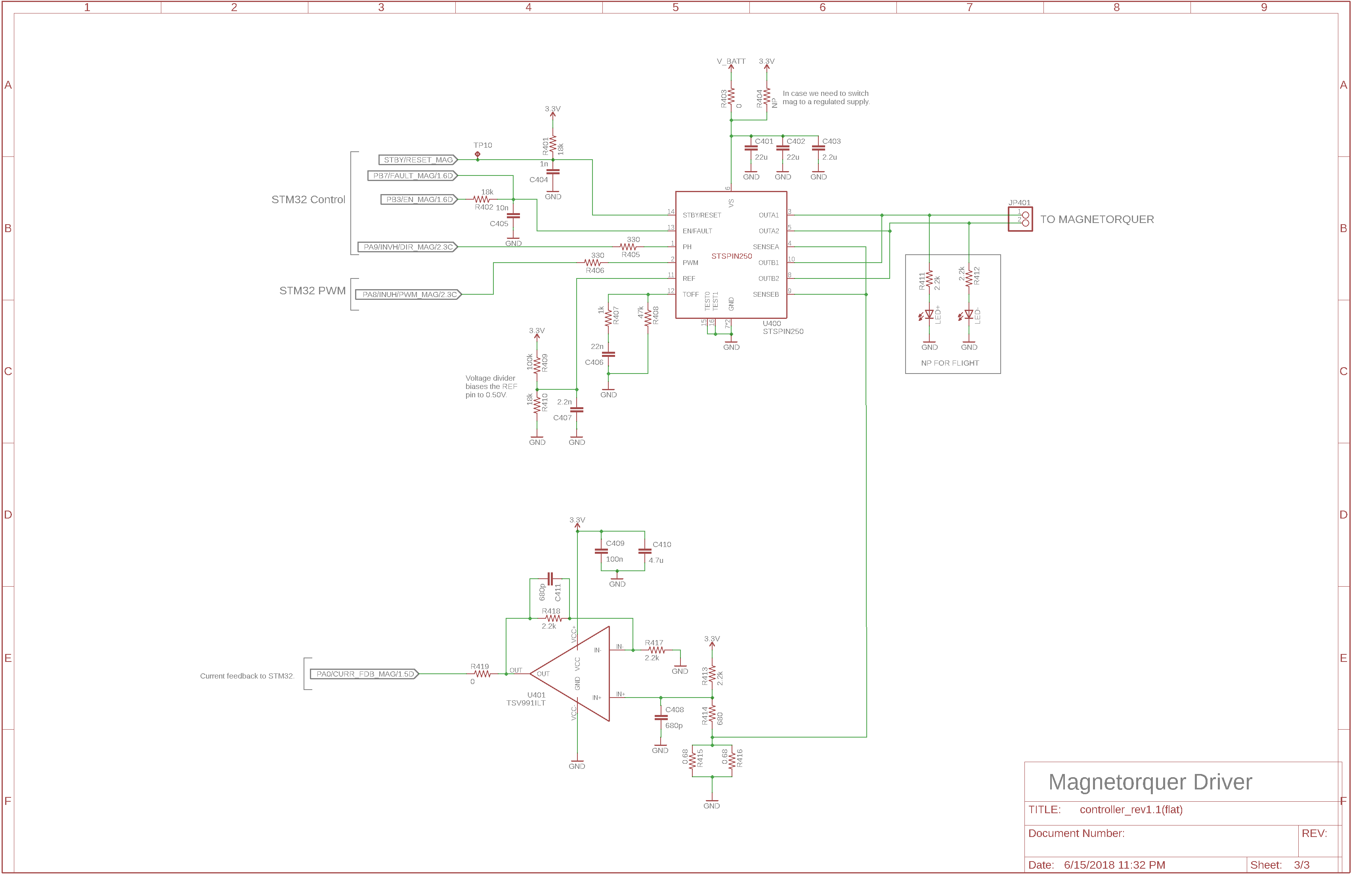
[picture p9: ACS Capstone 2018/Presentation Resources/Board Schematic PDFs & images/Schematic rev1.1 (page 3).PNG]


Rev2:
* Minor changes. Rev2 was never manufactured. Skip and go reference Rev3.
 
Rev3:
* Rev3 was manufactured and tested.
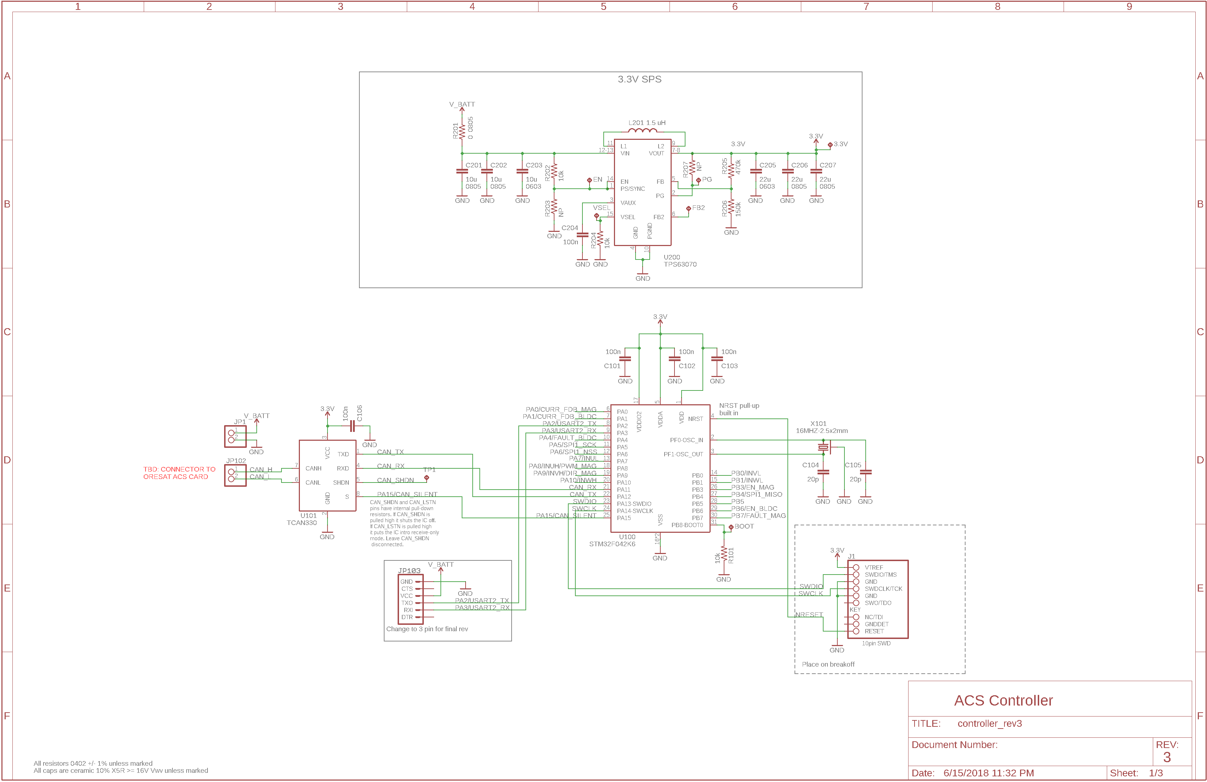
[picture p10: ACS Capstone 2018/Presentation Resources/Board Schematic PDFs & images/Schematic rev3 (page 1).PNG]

**Note:** R206 must be changed from 100kΩ to 150kΩ.
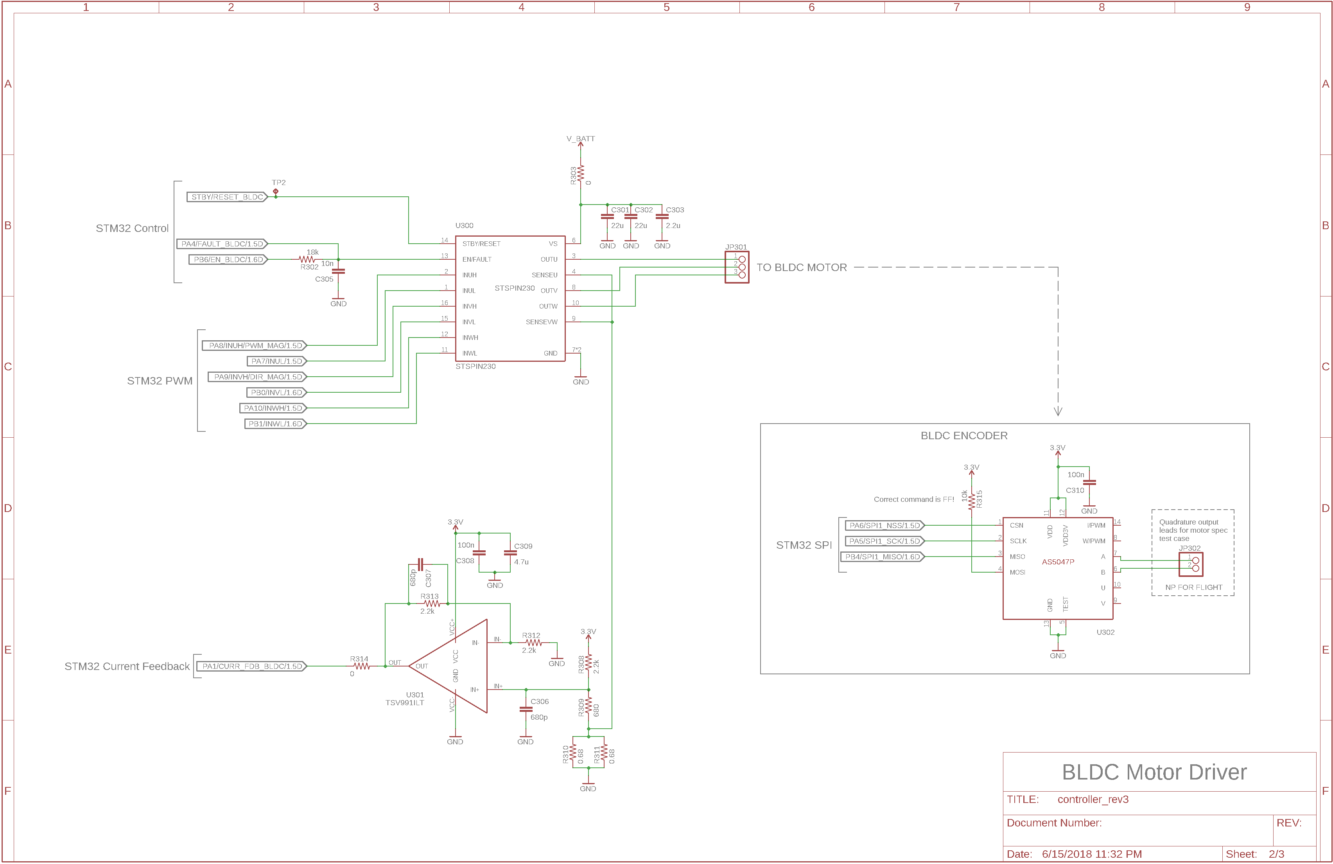
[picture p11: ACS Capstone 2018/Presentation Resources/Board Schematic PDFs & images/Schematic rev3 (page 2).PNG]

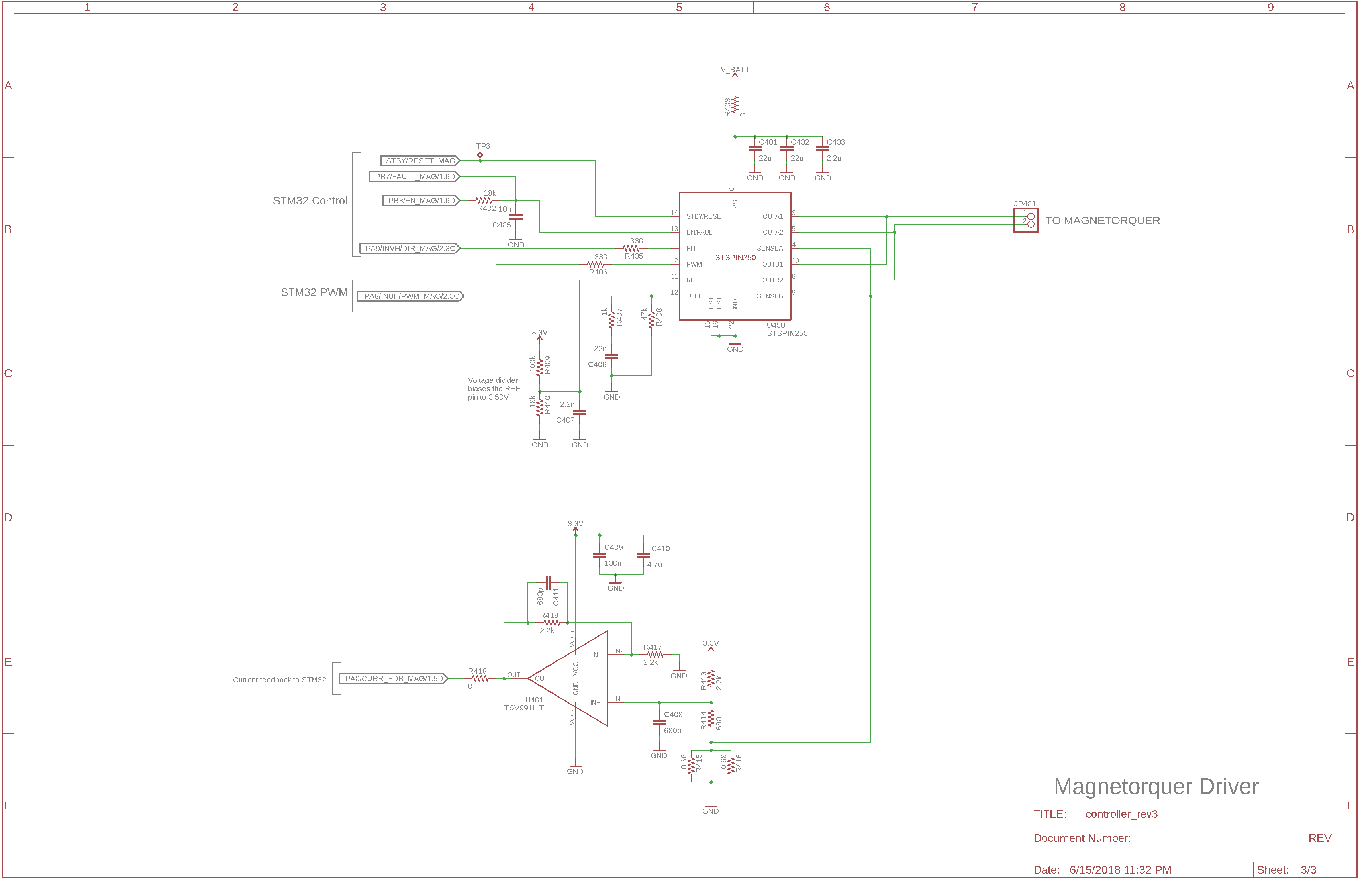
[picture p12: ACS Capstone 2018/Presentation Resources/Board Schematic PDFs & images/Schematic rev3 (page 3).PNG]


## Board Layout
* The design of the board layout was a significant hardware challenge due to the physical space constraints in the cubesat. Our entire system needed to fit within a volume of 10x10x4 cm. Our system needs to drive four BLDC motors and three magnetorquers. Additionally, each motor needs an encoder positioned right next to it in line with the motor’s axle. 
* Our proposed solution was to design a board that contains all the hardware needed to drive a single BLDC motor, a single magnetorquer, run the encoder, and also run the CAN communication. We’d use four of these boards to run all four BLDC motors and also the three magnetorquers. Having a single board for each BLDC motor allows us to mount the encoder directly on the board and then mount the board directly in line with the motor’s axle.
* The volume constraints drove us to create our board layouts as compact as possible.

**REV1:** <br/>The goal of REV1 was to make a very compact board as a prototype so that we could get a good idea of how much area our board will take up. REV1 ended up with an area of 42x43mm. We passed this information onto the structure team so they could start prototyping how to fit everything into the cubesat frame.

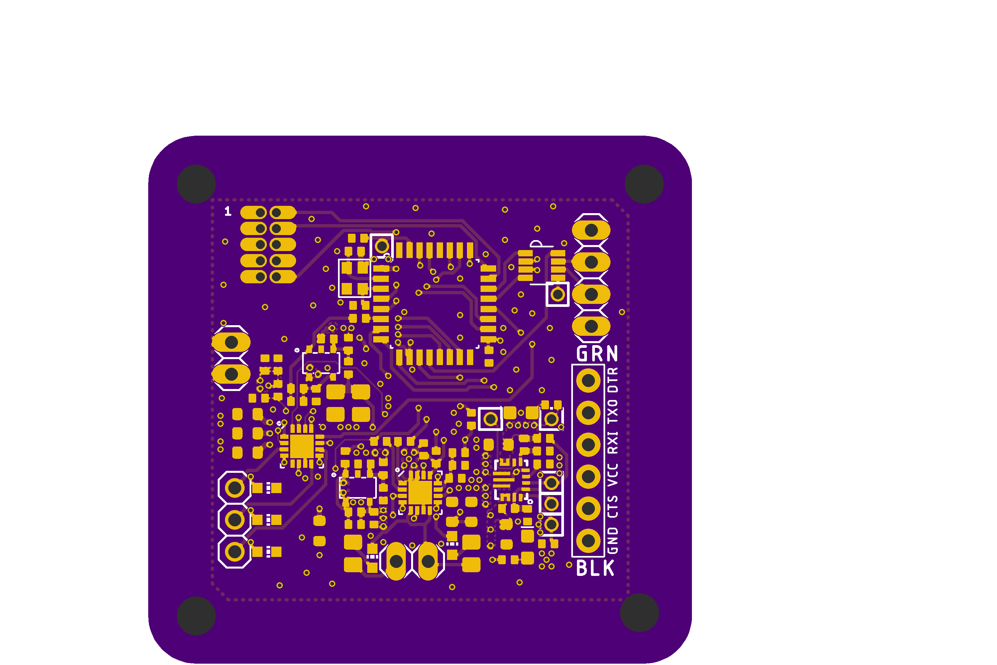
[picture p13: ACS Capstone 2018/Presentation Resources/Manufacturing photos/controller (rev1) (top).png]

_Rev1: Top_
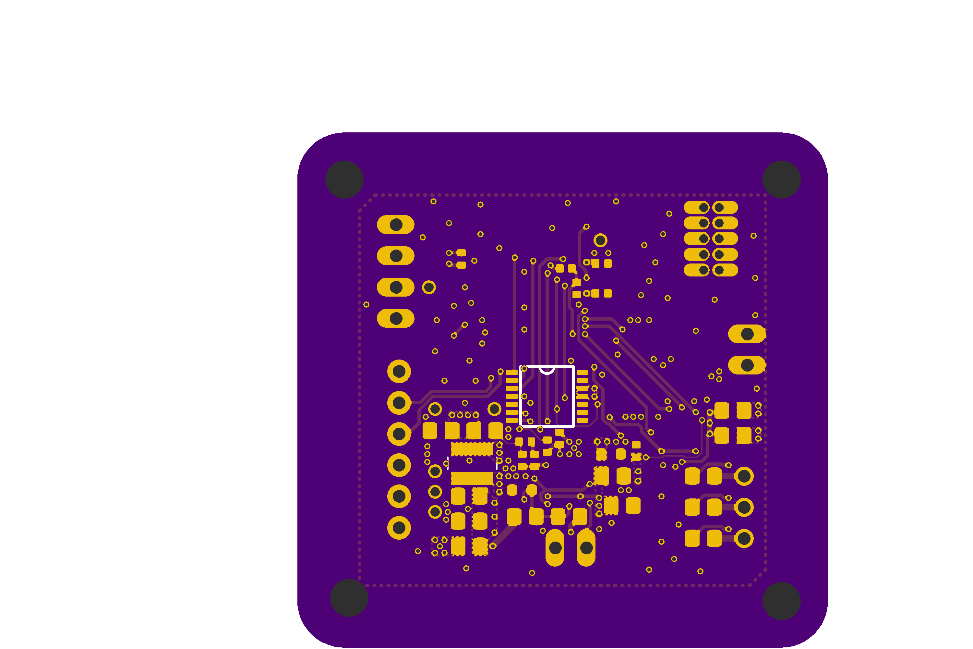
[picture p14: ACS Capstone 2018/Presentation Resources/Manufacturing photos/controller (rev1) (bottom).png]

_Rev1: Bottom_

**Rev1.1:** <br/>The goal of REV1.1 was to test all the hardware components and prove that they would work when all integrated together. REV1 was manufactured and assembled. All the hardware worked as expected with only minor design errors discovered.

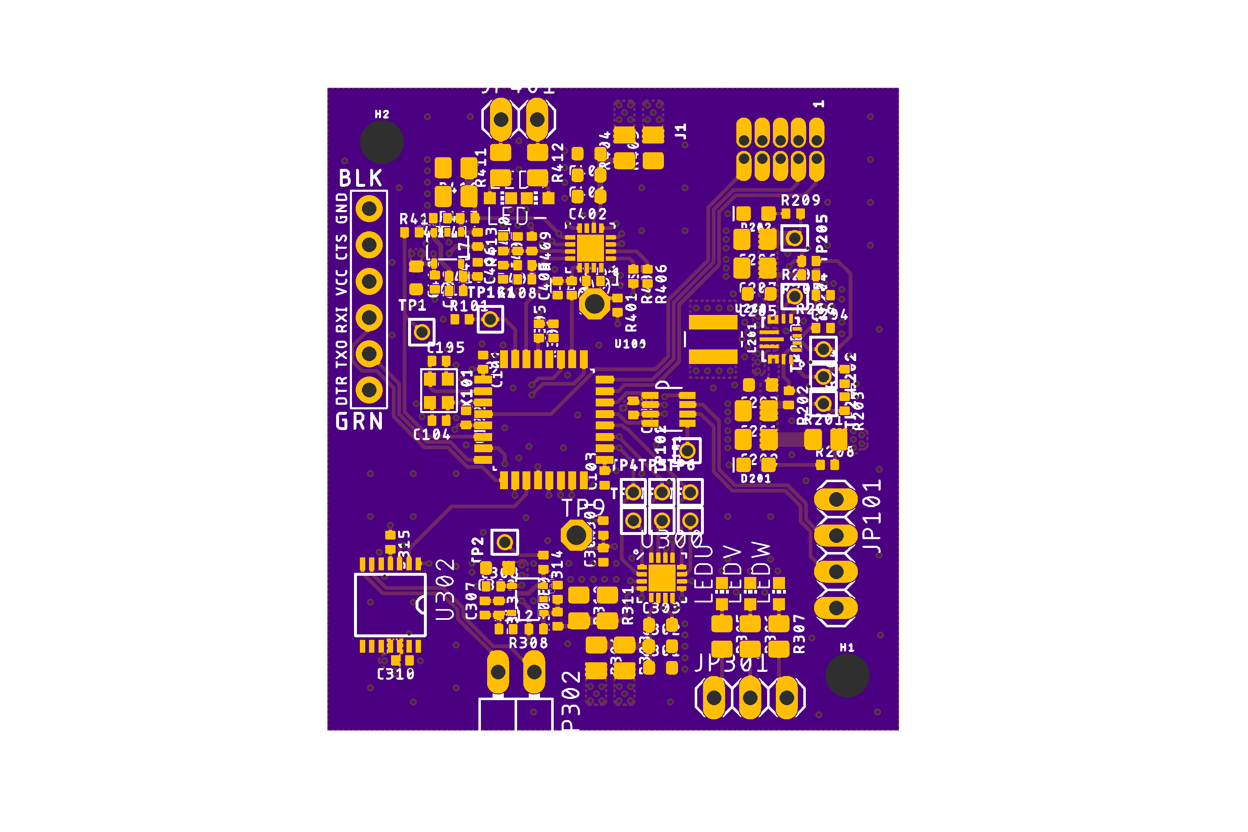
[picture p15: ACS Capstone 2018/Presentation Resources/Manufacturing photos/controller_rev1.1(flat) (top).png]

_Rev1.1: Top_
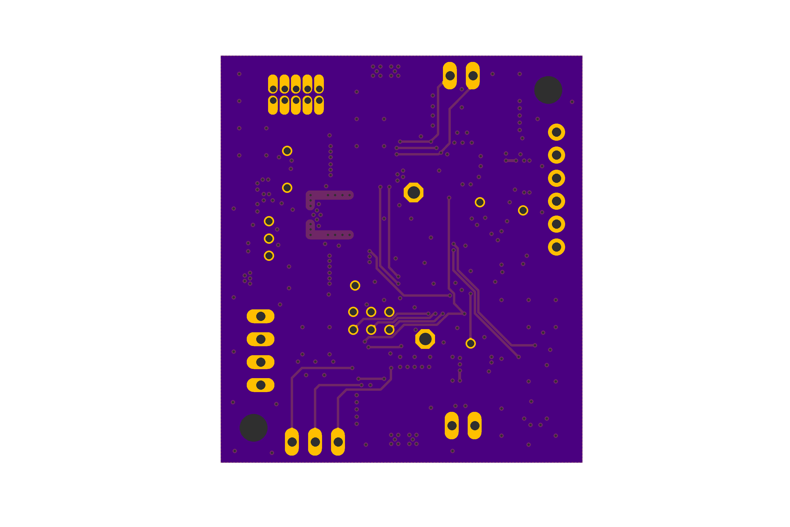
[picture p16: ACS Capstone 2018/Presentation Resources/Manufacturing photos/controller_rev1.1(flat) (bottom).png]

_Rev1.1: Bottom_

**Rev2:** <br/>The goal of REV2 was to get a head start on developing better packing geometries that utilized both top and bottom layers for component placement. Upon reviewing the design for developing a mechanical mount, it was determined that with how effectivly the space was used, size should be deprioritized in favor of how it was to be mounted. This layout was then abandoned due to the amount of modification necisary for the mounting system that was developed shortly after.

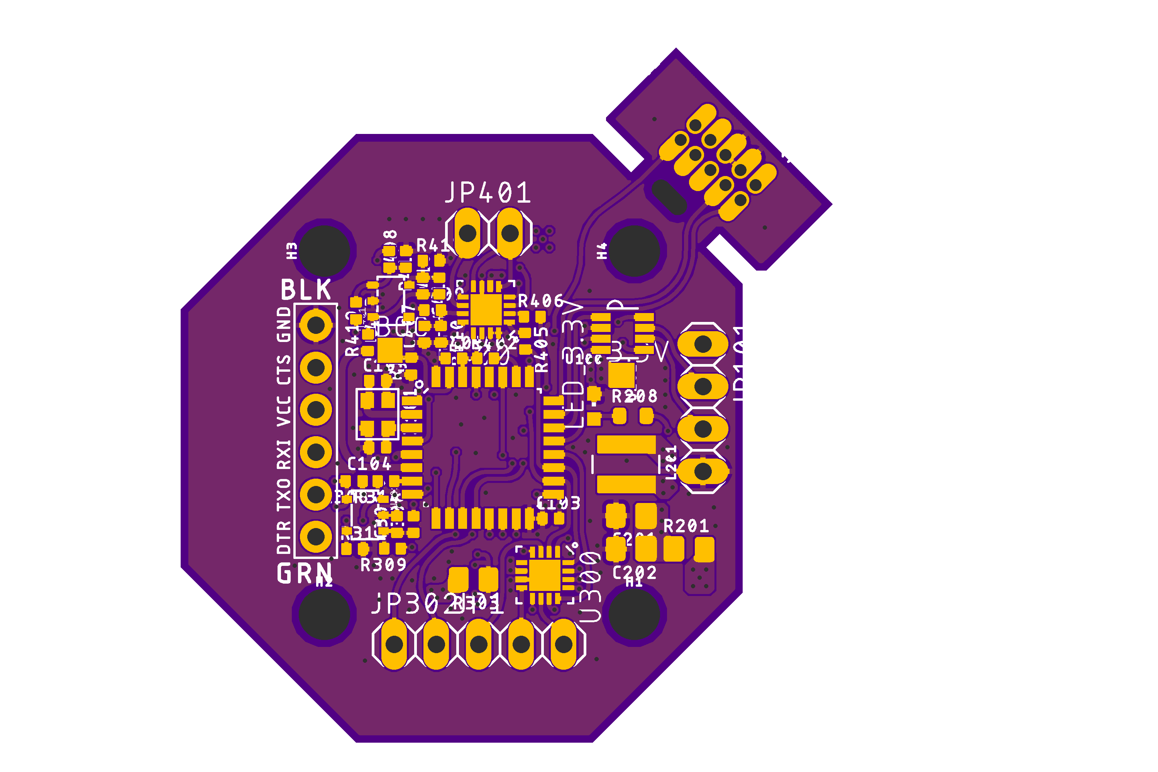
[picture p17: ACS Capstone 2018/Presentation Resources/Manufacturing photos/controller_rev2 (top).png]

_Rev2: Top_
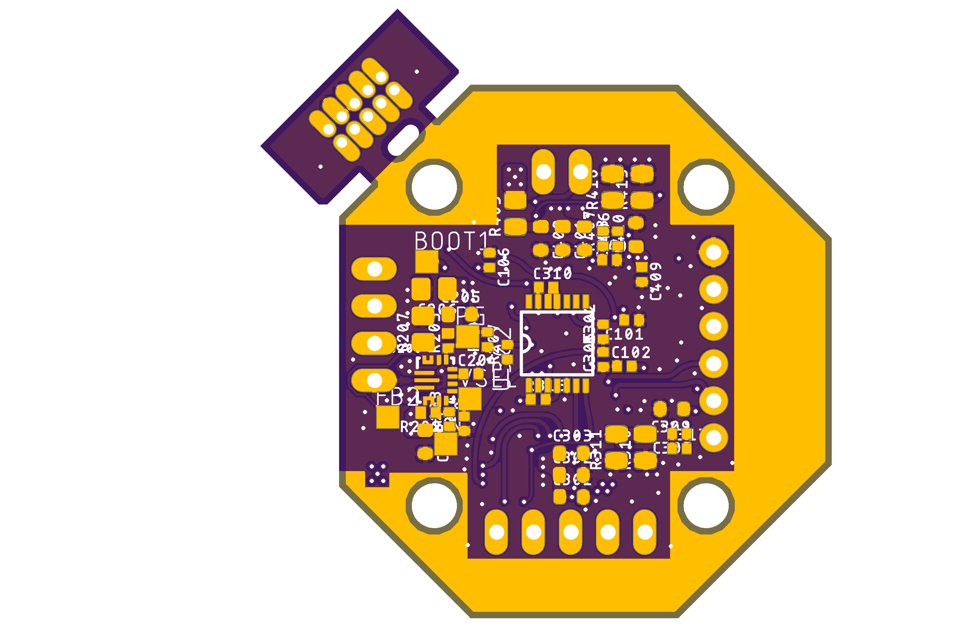
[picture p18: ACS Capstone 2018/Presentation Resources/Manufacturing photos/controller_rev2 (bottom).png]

_Rev2: Bottom_

**Rev3:** <br/>We received input from the structural team which informed us that we need to redesign the shape of the board and change the locations where thermal contacts occurs. The total area of REV3 came out to be a very small 38x35mm. 

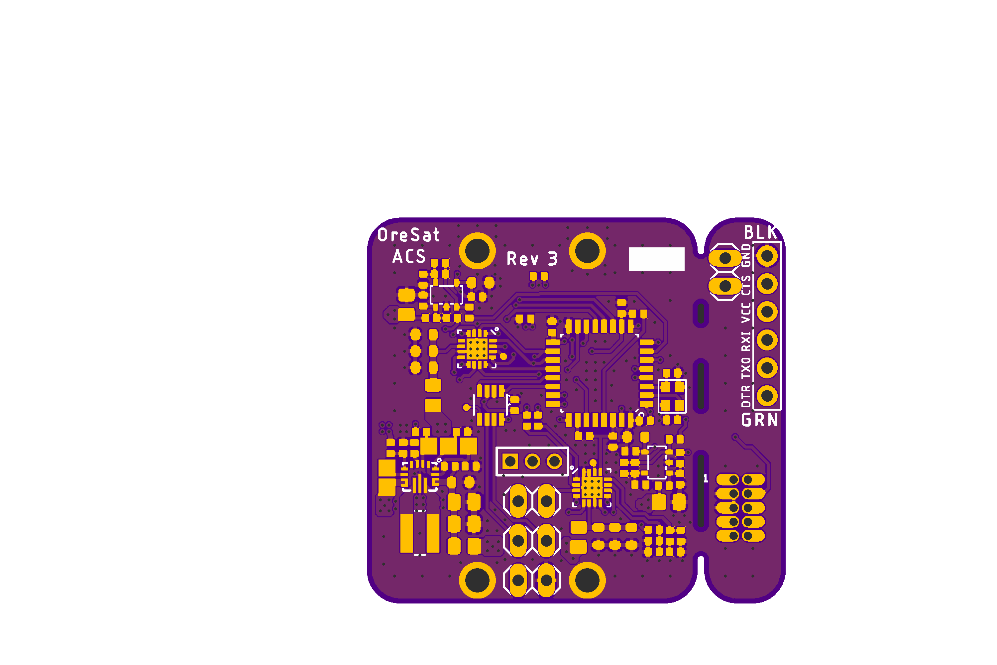
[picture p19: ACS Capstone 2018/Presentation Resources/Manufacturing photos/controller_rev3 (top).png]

_Rev3: Top_
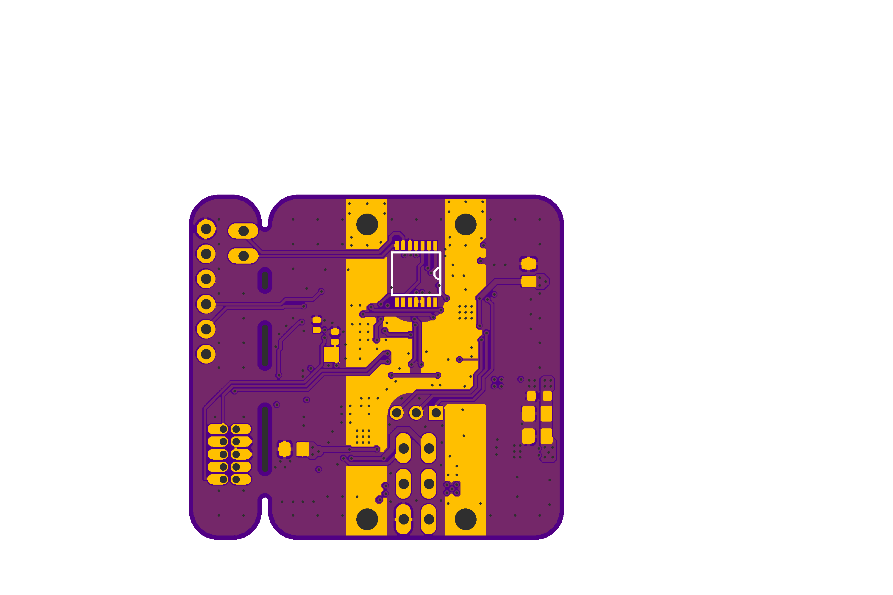
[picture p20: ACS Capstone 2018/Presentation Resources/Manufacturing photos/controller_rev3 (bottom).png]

_Rev3: Bottom_ 

## CAD photos for satellite mounting: 
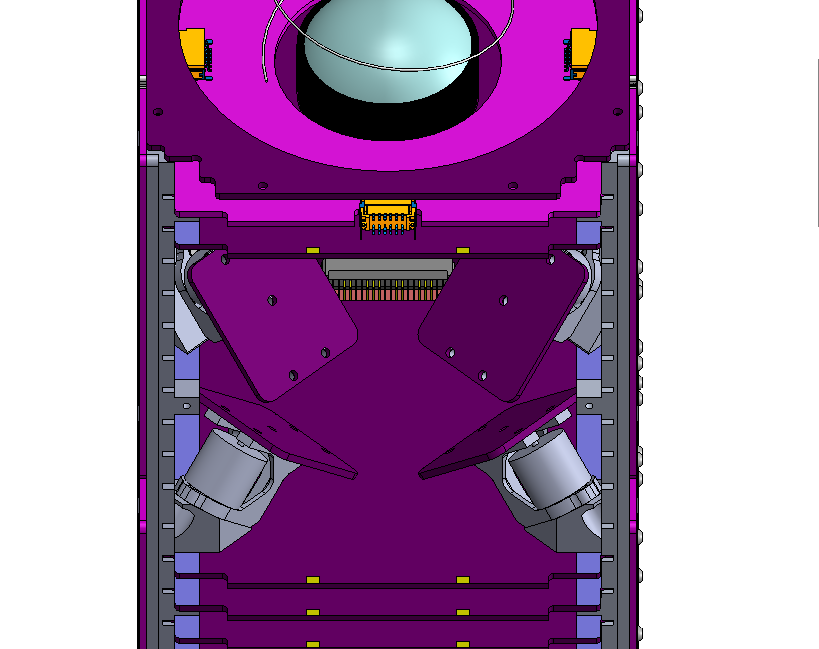
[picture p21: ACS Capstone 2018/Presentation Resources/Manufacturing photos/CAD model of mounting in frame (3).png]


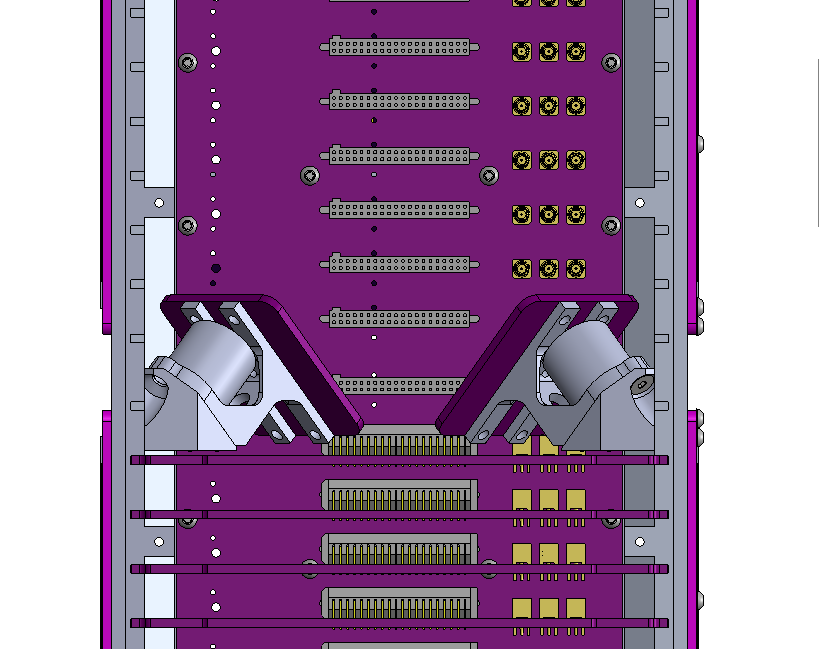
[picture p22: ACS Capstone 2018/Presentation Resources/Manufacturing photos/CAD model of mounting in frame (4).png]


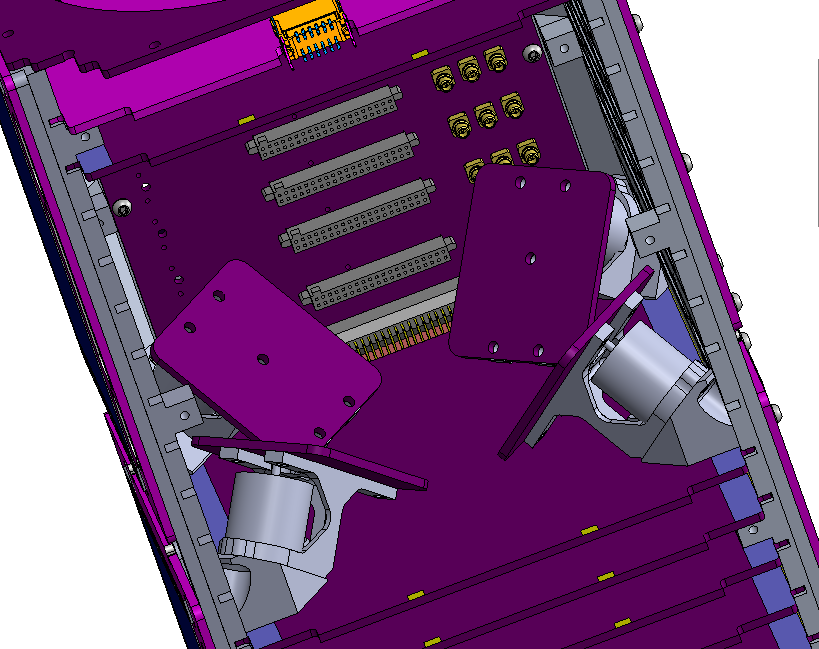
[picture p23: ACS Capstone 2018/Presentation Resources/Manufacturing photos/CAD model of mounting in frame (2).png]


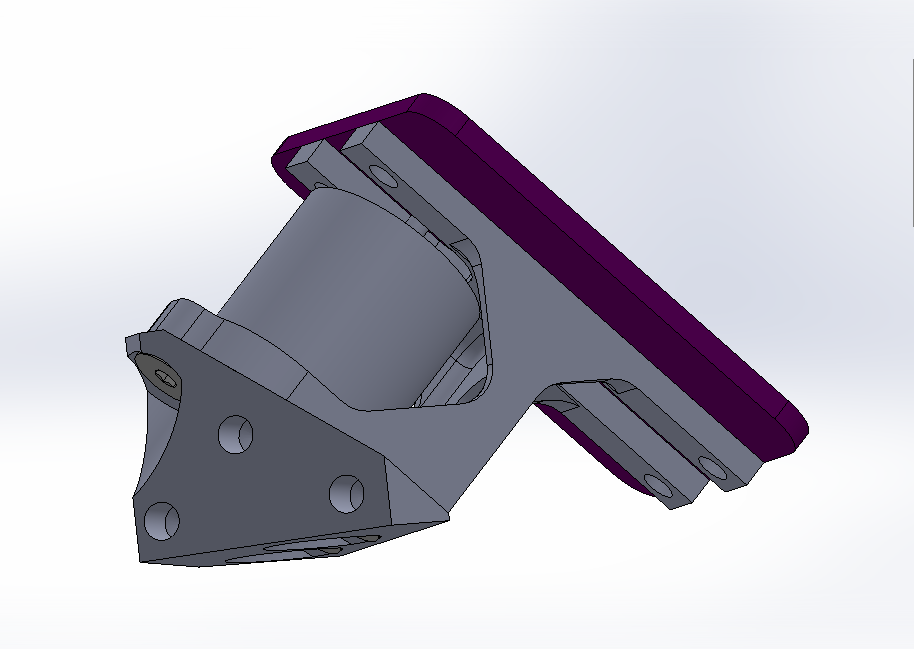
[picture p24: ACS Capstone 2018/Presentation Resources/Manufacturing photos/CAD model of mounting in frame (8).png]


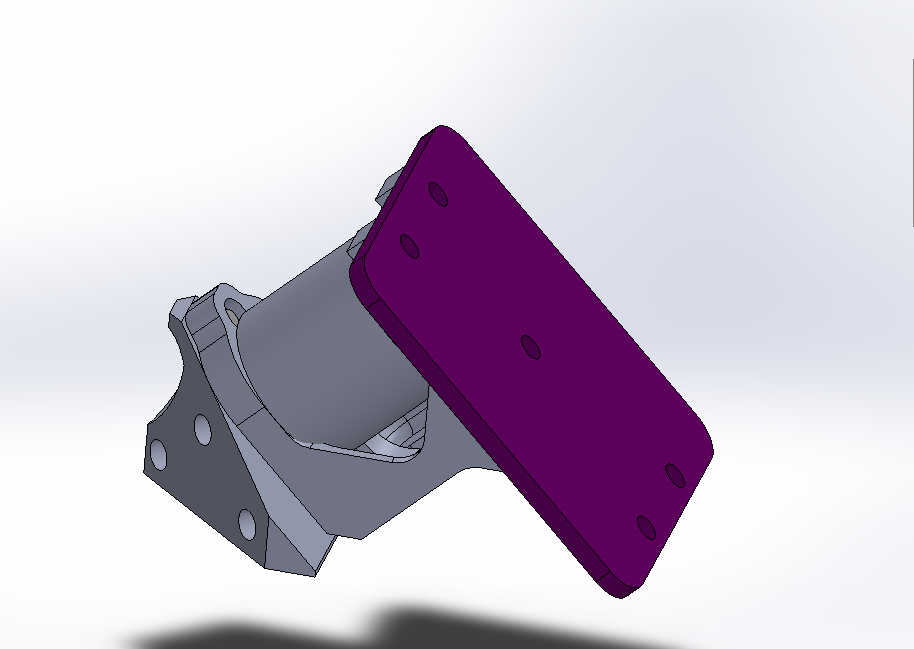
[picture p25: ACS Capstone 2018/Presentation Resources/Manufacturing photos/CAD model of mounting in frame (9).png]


# Board Stuffing SoP

Both Rev1.1 and Rev3 can have the top side fully stuffed and baked in the reflow oven.
1. Prepare all tool and supplies: Tweezers, solder-paste, napkins, surface mount components, schematic and board layout references.
2. Prepare solder-paste stencil: Place the bare PCB on the table and place the L-shaped supports around it. The L-shaped supports should come with the solder stencil. Tape the supports to the table so they do not slide around. Now align the solder stencil on top of the board and tap the stencil down to the L-shaped supports so that the stencil does not slide around. Apply solder-paste and squeegee/scrape off the excess.
3. Organize surface mount components in whatever is most convenient.
4. Place components one by one on the board with tweezers by referencing the board layout. This is the super long tedious part. Be patient. It’s better to work slow than to mess up. You don’t want to clean a pasty mess.
5. After all the components are placed, carefully remove the board and inspect everything visually under a microscope. Make small alignment fixes where necessary.
6. Carefully place the board in the reflow over and follow reflow procedure.
7. Remove board (CAUTION - HOT). Inspect visually with the microscope. Look for solder bridging. Reflow and remove solder where necessary. Pro tip 1: look at tricky components at an angle so you can see underneath them better. Pro tip 2: use the Metcal solder station. It dumps heat very quickly and regulates its temperature well.
8. Proceed to stuff the bottom of the board by hand with the solder iron. Pro tip 3: don’t use solder irons with tiny tiny tips. The tips rarely get hot enough to melt solder properly. Pro tip 4: For soldering surface mount resistors and capacitors; tin one pad with solder and leave the other one clean. Bring the component close with tweezers in one hand and with the other hand use the iron to reflow the solder while aligning the component into its place. Solder the other pad once the component is being held in its proper place. A similar method should be used for an mcu. Only tin one pad. Aling and place the mcu. That one pad will hold it aligned in place. Then solder the rest of the pins. Don’t worry if you bridge. The Metcal is good at heating up braid for removing solder bridging.
9. Congrats! You are done. Now you can move on to testing and debugging.

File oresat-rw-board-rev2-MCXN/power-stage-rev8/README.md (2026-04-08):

---
title: "**MCXN-Reaction-Wheel-Board-V2**"
subtitle: |
  **Fabrication and Assembly Information**\
  For build TIME-STAMP
fontsize: 10pt
geometry:
  - margin=0.5in
toc: true
toc-depth: 2
colorlinks: true
urlcolor: blue
---

\newpage

# About this Board

## Board Description

The MCXN-Reaction-Wheel-Board-V2 is the dedicated controller board for the reaction wheel assembly. Each controller manages a single reaction wheel. Centered around the NXP MCXN947VDFT microcontroller, this board combines:

- GaN H-bridge inverters for motor driving
- Current sense amplifiers
- Encoder interfacing
- Additional thermal and voltage metrology
- Communication to the ADCS Card

## Documentation Links

- ADCS hardware Git repository: <https://github.com/oresat/oresat-adcs-hardware>

## Documentation Files

| Filename | Notes |
| --- | --- |
| README.pdf | This README file |
| PROJECT-NAME-outline.dxf | Board outline (with holes) in DXF format |
| PROJECT-NAME-pcba.step | 3D model of PCBA (with components) |
| PROJECT-NAME-render-top.jpg | Render of the top of the 3D model |
| PROJECT-NAME-render-bot.jpg | Render of the bottom of the 3D model |
| PROJECT-NAME-schematic.pdf | PDF of board schematics |

## Board Renders

Render of the top of the 3D model
Render of the bottom of the 3D model

\newpage

# Printed Circuit Board (PCB) Fabrication Information

## Board Info

- 6-layer board
- Bounding box is approximately 50 x 33.5 mm 
- Board thickness is 1.6 mm 
- **Important:** See Materials section below
- 
## Board Requirements

- Design Rules
    - Minimum Trace width: 0.1 mm
    - Minimum Clearance/Space: 0.1 mm
- Drills and Vias
   - Via Diameter: 0.20 mm
   - Minimum Annular Width: 0.07 mm
- Outline/Routing
  - Requires a routing bit suitable for the 50x33.5mm profile.
- If not otherwise specified, build to IPC 6012 Class 2 or better. High precision is required across all fabrication steps.

## Materials

- Dielectric Material: Standard FR4
- Board Surface Treatment: ENIG (Electroless Nickel Immersion Gold)
- Controlled Impedance: None required

## Fabrication Files

### IPC-2581 File

| Filename | Notes |
| --- | --- |
| PROJECT-NAME-ipc2581.xml | IPC-2581 board information file |

### Legacy PCB Files (Gerbers/Drills)

| Filename | Notes |
| ---| --- |
| PROJECT-NAME-Edge_Cuts.gbr | RS274X file for the dimension (outline) layer |
| PROJECT-NAME-F_Silkscreen.gbr | RS274X file for the top silkscreen |
| PROJECT-NAME-F_Mask.gbr | RS274X file for the top soldermask |
| PROJECT-NAME-F_Cu.gbr | RS274X file for the top copper layer |
| PROJECT-NAME-In1_Cu.gbr | RS274X file for the layer 2 copper |
| PROJECT-NAME-In2_Cu.gbr | RS274X file for the layer 3 copper |
| PROJECT-NAME-In3_Cu.gbr | RS274X file for the layer 4 copper |
| PROJECT-NAME-In4_Cu.gbr | RS274X file for the layer 5 copper |
| PROJECT-NAME-B_Cu.gbr | RS274X file for the bottom copper layer |
| PROJECT-NAME-B_Mask.gbr | RS274X file for the bottom soldermask |
| PROJECT-NAME-B_Silkscreen.gbr | RS274X file for the bottom silkscreen |
| PROJECT-NAME-NPTH.drl | Excellon file for non-plated through holes |
| PROJECT-NAME-PTH.drl | Excellon file for plated through holes | 

\newpage

# Printed Circuit Board Assembly (PCBA) Information

## Assembly Info

- Double-sided assembly (components on both Top and Bottom sides).
- Exclusively Surface Mount Technology (SMT) components; no Through-Hole (THT) parts.

## Assembly Requirements

- **Precision:** Extreme precision is required for all placement and reflow operations due to the density and component types (GaN, MCXN947VDFT).
- Assemble to IPC Class 2 or better.
- Solder paste **MUST** be leaded.
- Aqueous flux and wash strongly preferred.
   - Clean to NASA Standard "Visibly Clean (VC)": No particles or residues are visible to the naked eye.
- Ship in antistatic protective bags.

## Assembly Files

### IPC-2581 File

| Filename | Notes |
| --- | --- |
| PROJECT-NAME-ipc2581.xml | IPC-2581 board information file |

### Bill of Materials (BOM)

| Filename | Description |
| --- | --- |
| PROJECT-NAME-bom.csv | BOM in Comma Separated Variable format |

### Solder Paste Stencils

| Filename | Notes |
| --- | --- |
| PROJECT-NAME-B_Paste.gbr | RS274X file for bottom/back solder paste stencil |
| PROJECT-NAME-F_Paste.gbr | RS274X file for top/front solder paste stencil |

### Mounting/Placement Location

| Filename | Description |
| --- | --- |
| PROJECT-NAME.pos | Pick and place locations for components |

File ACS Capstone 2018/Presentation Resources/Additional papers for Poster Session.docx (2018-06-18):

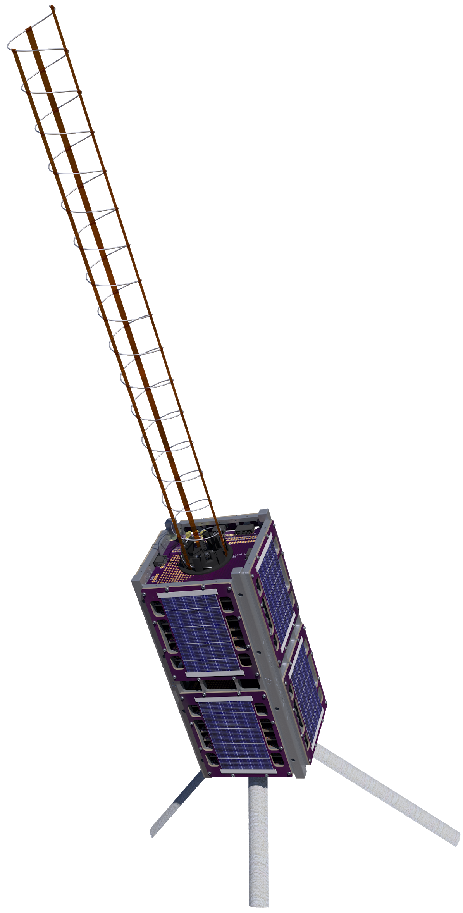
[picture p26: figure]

OreSat

Attitude Control System

(ACS)

Top view of four ACS boards in flight configuration

OreSat bus

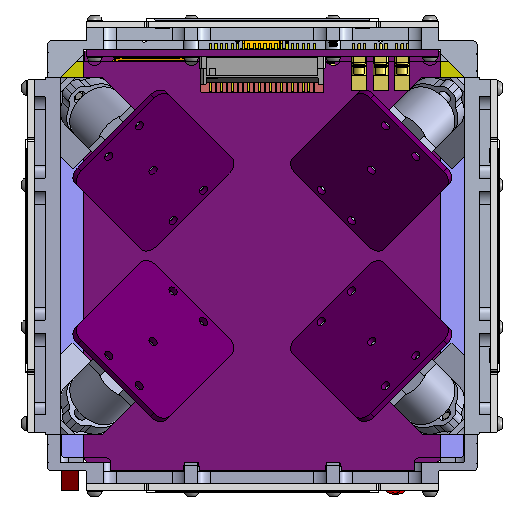
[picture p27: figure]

Only three motors will be needed for full 3-axis control. Four motors allows redundancy in case one ACS board or motor fails while in orbit.

Side view of two ACS boards in flight configuration

OreSat bus

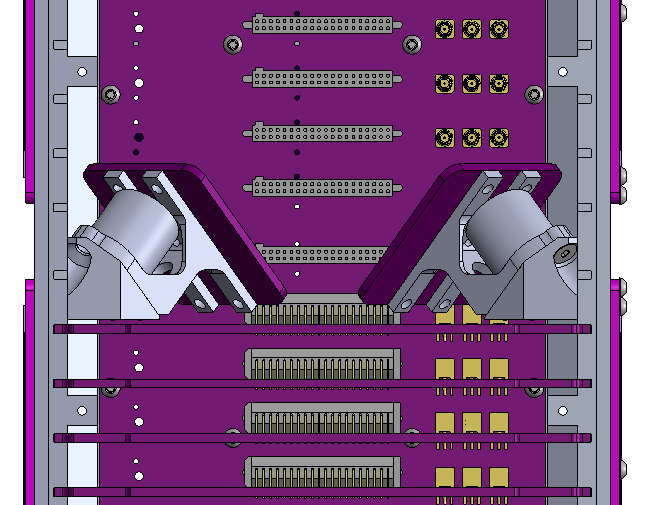
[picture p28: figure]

The motors will be situated in a ring half-way up the satellite. Like every other component of the satellite, the ACS assembly will be modular. The “card” it is on will be able to slide in and out of the frame for easy assembly. The ACS assembly will take four “cards” worth of space.

Reaction Wheel Controller (one per ACS board)

Phase-vector control uses sinusoidal waveforms.

We generate the three sinusoidal waves using six Pulse-Width Modulation (PWM) signals, one for each phase, and one for each phase complimented.

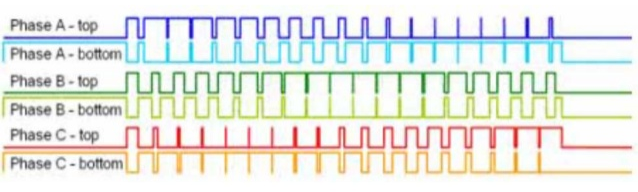
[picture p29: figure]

The six PWM signals are fed into a triple-half H-bridge, which sends current into the Brushless-DC (BLCD) Motor.

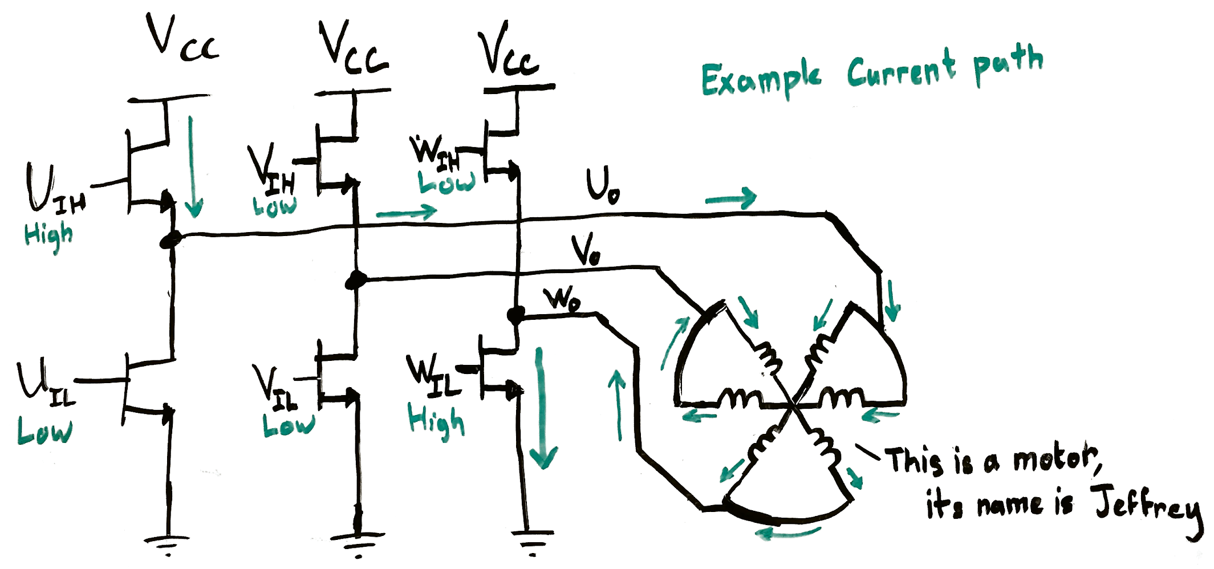
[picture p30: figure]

Magnetorquer Controller (one per ACS board)

Magnetorquers are inductors, and can be controlled with an H-bridge.


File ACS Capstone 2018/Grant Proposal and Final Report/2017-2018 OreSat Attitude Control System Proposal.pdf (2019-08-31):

# OreSat Attitude Control System

An application for the Oregon Space Grant Consortium 2017-2018 Undergraduate Team Experience Award Program


Team Lead
Eric Ruhl
Undergraduate Student
Department of Electrical and Computer Engineering 215 E. Berkeley St., Gladstone, OR 97027
(503) 502 9650
eruhl@pdx.edu

Faculty Advisor
Dr. James McNames
Department of Electrical and Computer Engineering Portland State University
(503)725-5390
mcnames@pdx.edu

Date of Submission: 2017-11-10

Project Description
We propose to design, prototype, and test the Attitude Control System (ACS) of Oregon's first satellite, OreSat.

OreSat is a CubeSat with a 2U form factor that will be deployed into low earth orbit in late 2019 as part of the NASA CubeSat Launch Initiative. OreSat's primary mission is to connect Oregon K-12 students through space-based STEM outreach. OreSat will be transmitting live video from space. Oregon students will receive the signal with hand-built, hand-held radio receivers pointed at the satellite. OreSat's secondary mission is to survey of the global coverage of high altitude cirrus clouds using an inexpensive and innovative camera and filter system from Dr. Greg Bothun at the University of Oregon.

OreSat requires 3 axis attitude control for two reasons: to accurately point its high gain S-band (2.4 GHz) antenna, and to point its multi-spectral cirrus cloud camera system. OreSat requires a minimum pointing accuracy of only ± 5° with a target of ± 1°, which is a very wide target: most commercial off the shelf (COTS) ACS systems have accuracies in the arcseconds, although they usually cost more than $50,000.

For this project, we propose to design a low accuracy (± 1°), open source, and inexpensive attitude control system. In low earth orbit, there are several ways to control attitude, including reaction wheels, magnetorquers, and gas jet reaction control systems. After initial research, we have decided to combine reaction wheels for dynamic control and magnetorquers for detumbling and reaction wheel desaturation.

The ACS, a combined RW and MT systems, can have its requirements broken down into three areas: mechanical systems, RW motor control, and MT control. Mechanical requirements will include motor mounting positions, selecting motors that are appropriate for operation in a vacuum, can handle the high vibrational loads of testing and launch, and confirming that the final structure falls within CubeSat design restrictions of volume and weight. RW motor control will need to be able to operate any number of motors, being capable of applying positive or negative angular acceleration. It will also need to be able to accurately handle both very low and very high speeds, which will require phasor vector control. MT control will have to smoothly and accurately create north and south magnetic fields based on the Earth's local magnetic field in orbit.

Note that the attitude determination system (ADS) (the combination of a star tracker and GPS receiver) and the state space attitude control algorithm are separate OreSat projects being implemented by other teams, and are not considered here.

In this project, we will:

Determine RW Motor Configuration and Placement
We will explore several motor configurations. Although only three RWs are necessary to control the satellite, a four RW tetrahedral arrangement has been used in CubeSats in the past to provide n+1 redundancy in the RW system. We will research both configurations, and choose one that fits energy, angular momentum, and reliability requirements.

Select and test a RW Motor
While this could simply be solved by purchasing extremely expensive space-rated motors, we still aim to be an inexpensive, open source project. This means doing things the hard way if it reduces cost and thus allows more people access to technologies. We will research the requirements and challenges of space-rated motors, and then choose a series of off-the-shelf DC brushless motors which we think may either directly be usable, or through some small modification (e.g., vacuum rated grease), be able to be used in orbit.

Create a RW Motor Controller Board
We will design a small, lightweight, vacuum-rated DC brushless motor controller to control the RWs. These boards will receive motor velocity commands from OreSat's Controller Area Network (CAN) control bus, and create the waveforms necessary to control the motor at that speed. It will also have an absolute position encoding in order to accurately control the motor at very low speeds.

Create a MT
While MTs are solenoids -- simple coils of wire that generate magnetic fields -- they must work in the vacuum of space, and should be built to be as efficient and lightweight as possible. We will research coil materials and choose the coils geometry based on these requirements.

Create a MT Controller Board
We will design a small, lightweight, vacuum-rated MT controller to control the current (and thus magnetic field) of the MTs. These boards will receive current commands from OreSat's CAN bus, and use a pulse-width modulated (PWM) Full H-bridge controller in order to be able accurately control current in either direction.

Test, Test, Test.
All CubeSat systems must meet the CubeSat Design Specification and go through a series of environmental tests, including vibration table shake and several thermal vacuum cycles. The first prototypes will be tested for both shake resistance and the ability to operate at full power in a thermal vacuum chamber. Since we lack the facilities to run these tests, we will be reaching to local industry for help.

Figure 1, below, shows some initial ideas for reaction wheel placement in the 2U OreSat.

Figure 2, below, shows a brushed motor reaction wheel prototyping system that "flew" in the PSU Dryden droptower as a proof of concept of the tetrahedral arrangement of motors.

Table 1 shows our project plan, with key milestones.


Figure 1: CAD rendering of RW system inside 2U OreSat


Figure 2: 2016-2017 DC brushed motor RW prototype system.

Table 1: Project plan, with Key Milestones and Deliverables (12/01/17 - 06/10/18)
12/01 - 1/31 | Research reaction wheels (RWs) and magnetorquers (MTs). Figures of merit, control systems, requirements, COTS options, MT materials, RW motor options, etc. Write up a Product Design Specification (PDS) and present it at a Preliminary Design Review(PDR).
2/1 - 2/28 | "Breadboard prototype" of first reaction wheel/magnetorquer drive board. Driver electronics de-risked. First tests of motors in a thermal vacuum chamber.
3/1 - 3/31 | First prototypes of PCBs. Fully operational RW and MT control. First vibration tests with full system. Critical Design Review (CDR) after the first tests.
4/1-4/30 | Second prototype PCBs, and first full RW + MT system for all three axes. System vibration and environmental testing.
5/1 - 5/31 | Integrate full system with prototype closed loop control from OreSat Attitude Control Project. Test for detumbling on air bearings.
6/1 - 6/29 | More system tests; lifetime tests in a thermal vacuum chamber. Final documentation.

Scholarly Aspects and Educational Objectives
The ACS will give participating students deep experience in interdisciplinary student projects. EEs, MEs, and CS students will be working together on a critical subsystem of an aerospace vehicle. We expect several AIAA and IEEE AESS student papers to come out of this project.

Synergy

Team-Advisor Collaborative Learning
We are excited to work with Dr. McNames on this project. Dr. McNames is the chair of the ECE department and has run student capstone projects for years. His specialty is signal processing of MEMs accelerometers and gyroscopes in order to get orientation estimates of wearable sensors, so he is intimately familiar with the problems and pitfuls aof attitude estimation and control. Dr. McNames has also worked on several aerospace projects, including health monitoring of helicopters using vibration sensors. Similarly, we hope to add MEMs accelerometers directly to the motor housing so we can pick up whether or not a motor is failing.

Additionally, Dr. McNames is one of the faculty advisors for the Portland State Aerospace Society, and has long been a strong supporter of these kinds of interdisciplinary student groups. He's been instrumental in providing resources and raising funds for the group.

Leveraging Opportunities for Funding or Further Research
The ACS system is the actuator necessary to test attitude determination and actual control theory on OreSat. It is the key piece of technology necessary to test the full closed loop attitude determination and control system (ADCS). We even expect several master's thesis projects to be enabled by this system.

It also dramatically impacts the academic CubeSat community; there simply is no inexpensive, open source ACS. This will enable smaller groups of students to be able to take on more meaningful satellite projects, since an attitude control is such a critical part of so many payloads.

Aerospace Relevancy
The ACS has obvious direct relevance to aerospace. First, novel, inexpensive technologies for small satellites fall directly under the guise of the Space Technology Mission Directorate (STMD). Several STMD funded Small Business Innovation Research (SBIR) grants have even gone to fund reaction wheels projects in the past. Second, lower cost ACSs will reduce ¹ the price of Earth observation CubeSats, which directly supports the mission of the NASA Science Mission Directory (SMD). And finally, the OreSat mission itself supports the NASA Education Directorate by both educating teams of undergraduate engineering students and most of the high schoolers in the state of Oregon in fall of 2019 after OreSat's launch.

1https://techport.nasa.gov/externalFactSheetExport?objectId=8154

Budget
This budget includes materials and services necessary to make 2 rounds of prototypes and 2 final flight versions of the OreSat Attitude Control System (ACS). It also includes in-kind services and donations in order to meet the 1.5x matching requirement.
Qty | Description | Vendor | Cost Ea. | Ext. Cost | Ext. Donation
10 | ST Micro STM32F042K6 dev boards | Digi-Key | $11.00 | $110.00
5 | ST Micro EVAL6235Q brushless motor driver boards | Digi-Key | $56.25 | $281.25
8 | Prototype Turnigy Multistar 22 Pole DC brushless motors (https://hobbyking.com/en_us/4108-480kv-turnigy-multistar-22-pole-brushless-multi-rotor-motor-with-extra-long-leads.html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) | Hobby King | $29.62 | $236.96
4 | Prototype machined reaction wheel rotational masses | ProtoLabs | $110.00 | $440.00
8 | Prototype PCBA components | Digi-Key | $100.00 | $800.00
8 | Prototype magnetorquer spindles | ProtoLabs | $95.00 | $760.00
8 | Flight model DC brushless motors | Maxxon Motors | $300.00 | $2,400.00
8 | Flight model PCBA components | Digi-Key | $100.00 | $800.00
8 | Flight model magnetorquer spindles | ProtoLabs | $175.00 | $1,400.00
1 | ADIS16485BMLZ IMU + Magnetometer | Digi-Key | $1,661.65 | $1,661.65
7 | Dr. McNames' time | PSU ECE Department | $114.50 | | $801.50
10 | Glenn LeBrasseur's time | TWaves Consulting | $150.00 | | $1,500.00
1 | OSH Park PCB donation | OSH Park | $5,000.00 | | $5,000.00
1 | Screaming Circuits PCB assembly services | Screaming Circuits | $6,000.00 | | $6,000.00
TOTAL | $8,889.86 | $13,301.50
| Match ratio: | 1.50

Team Lead Resume
Eric Ruhl
c/o Portland State Aerospace Society 1930 SW 4

th Ave #91, Portland, OR 97201 503.502.9650
eruhl@cecs.pdx.edu

EDUCATION

Bachelor of Science in Physics | Bachelor of Science in Electrical Engineering
Portland State University, Portland OR | Maseeh College of Engineering and Computer Science, Portland OR
Expected date of Graduation | Expected date of Graduation
June 2019 | June 2019

COURSE HIGHLIGHTS
Circuit and Transistor Analysis, Fourier Analysis, Classical and Modern Control, Electromagnetics, Solid State Physics

SOFTWARE & HARDWARE SKILLS
-Proficient in multiple computer languages including C, C++ and Python as well as assembly

EXPERIENCE

Electrical Maintenance Engineer
Precision Castparts Co. Airfoils | (March 2017 - Present)
-Upgraded on X-ray security card scanning system
-designed an X-ray chiller feed controller
-Repaired a serial marking machine
-added extra sensor peripherals to a caustic autoclave system and boiler clave system

Student Member
Portland State Aerospace Society | (April 2014 - Present)
-Recovery system
-Secured 1k Beta project grant allowing for flight weight redesign of original system
-Adapted firmware from alternate controllers to fit custom application
-Implemented line cutter ignition system into motor controller architecture
-Leadership Team
-IEEE AESS Chairman
-Secured a 2.5k grant to produce initial prototype for open source international satellite connected ground station pilot program.
-participated in an exploratory committee to develop methods for maintaining a consistent knowledge pool in high turnover groups.

Manager
Electronic Prototyping Laboratory | (September 2017 - Present)
-Assisted Students in design and manufacturing of electrical, electronic, and mechanical prototypes -Teaching Students how to used Equipment Such as Laser Cutter, PCB Routers, and specialized soldering equipment

Team Member Listing and Experience Profiles

Group Demographics:
- Male/Female Students: 3/2 (40%)
- Underrepresented minorities: None
- Veterans: None

Chad Coates: (Computer Engineering Undergraduate, PSU)
Experience developing Linux and Windows kernel drivers, embedded systems, and antimalware software. Proficient at programming in C/C++, ARM assembly, and Verilog. Worked as an alarm technician to install, troubleshoot, and maintain home security and automation systems.

Marie House: (Mechanical Engineering Undergraduate, PSU)
Experienced in 3D CAD design using Autodesk Inventor and Solidworks; as well as design for manufacturing, especially for laser systems and the manual mill and lathe. Able to complete data analysis using R and Matlab software. Also experienced in amateur rocket recovery design through the Portland State Aerospace Society and Laser Technician work through the Portland State Mechanical Engineering Department.

Jennifer Jordan: (Electrical Engineering & Physics Undergraduate, PSU)
Experience manufacturing frame and electronics assemblies for underwater remotely operated vehicles, laser cutter fabrication processes, electronics design, circuit layout, BLDC motor assembly, high-voltage isolation testing, environmental isolation of electronic components and connections, part specification testing, and IMU sensor assembly and selection.

Armaan Roshani: (Computer Engineering Undergraduate, PSU)
Experience designing and implementing hardware stress test environments, designing and prototyping electronics, programming in C/C++, Verilog, and ARM Assembly. Experience selecting and working with embedded 3D sensors, and manipulating Point Clouds (3D environment data) in data analysis software (Matlab, OpenCV, and Point Cloud Library). Physics workshop leader and tutor. Technical Director of an Event Production company.

Eric Ruhl: (Electrical Engineering & Physics Undergraduate, PSU)
Current IEEE AESS Chairman of the Portland State Aerospace Society. Acted as the engineering team lead for a mission industry competition facilitated by NASA through the NCAS program. Experienced with electrical and mechanical prototyping, as well as minor experience with circuit board layout and fabrication. Prior experience with custom application motor control through design and testing of the controller for a mechanically actuated stage separation ring.

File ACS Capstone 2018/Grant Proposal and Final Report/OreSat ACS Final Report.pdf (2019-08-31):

# OreSat Attitude Control System

## Final report for the Oregon Space Grant Consortium 2017-2018 Undergraduate Team Experience Award Program

July 30th, 2018

Team Lead
Eric Ruhl
Department of Electrical and Computer Engineering 215 E. Berkeley St., Gladstone, OR 97027
(503) 502 9650
eruhl@pdx.edu

Team Members
Chad Coates
Marie House
Jennifer Jordan
Armaan Roshani

With Special Thanks to
Andrew Capatina
Nathan Dusciuc
Max Schweitzer

Faculty Advisor
Dr. James McNames
Department of Electrical and Computer Engineering Portland State University
(503)725-5390
mcnames@pdx.edu

Supported in part through NASA/Oregon Space Grant Consortium, grant NNX15AJ14H

## Table of Contents

1. Project Description | 2
2 Requirements Gathering | 3
2.1 External Constraints | 3
2.2 Design Paradigm | 4
2.3 Maintainability | 4
3 Results | 5
3.1 Determined RW Motor Configuration and Placement | 5
3.2 Selected and tested a RW Motor | 7
3.3 Create a RW Motor Controller Board | 7
3.3.1 Hardware | 9
3.3.2 Firmware | 10
3.3.3 Communication over the CAN Bus | 11
3.3.4 BLDC Motor Control | 11
3.3.5 Sensors and Feedback | 12
3.3.6 Reaction Wheel and Control Card Mounting System | 12
3.4 Create a Magnetorquer (MT) | 13
3.5 Create a MT Controller Board | 13
3.6 Test, Test, Test | 13
4 Conclusion and Future Work | 14
5 References | 15
6 Final Budget | 16
A Appendix | 17
A.1 Terms and Definitions | 17
Bibliography | 18
OreSat Attitude Control System Final Report | Page 1 of 19

# 1. Project Description

We designed, prototyped, and tested an Attitude Control System (ACS) for Oregon's first satellite, OreSat.

OreSat is a CubeSat with a 2U form factor that will be deployed into low earth orbit in late 2019 as part of the NASA CubeSat Launch Initiative. OreSat's primary mission is to connect Oregon K-12 students through space-based STEM outreach. OreSat will be transmitting live video from space. Oregon students will receive the signal with hand-built, handheld radio receivers pointed at the satellite. OreSat's secondary mission is to survey the global coverage of high altitude cirrus clouds using an inexpensive, innovative camera and filter system from Dr. Greg Bothun at the University of Oregon.

OreSat requires 3 axis attitude control for two reasons: to accurately point its high gain S-band (2.4 GHz) antenna for the live video transmission, and to point its multispectral cirrus cloud camera system. OreSat requires a minimum pointing accuracy of only ± 5° with a target of ± 1°, which is a very wide target: most commercial off-the-shelf (COTS) ACS have accuracies in the arcseconds, although they usually cost more than $50,000.

For this project, we design a low accuracy, open source, and inexpensive attitude control system comprised of reaction wheels (RWs) and magnetorquers (MT). Most of the focus on this project was on the electronics system needed to run the DC brushless motors of the RWs and bidirectional current in the MT coils.

Note that the attitude determination system (ADS) (the combination of a star tracker and GPS receiver) and the state space attitude control algorithm are separate OreSat projects being implemented by other teams, and are not considered here.

In our proposal, we had a list of six deliverables. We're happy to say we delivered on 4 and partially delivered on 2:

1. Determined RW Motor Configuration and Placement -- DONE
2. Selected and tested a RW Motor -- DONE
3. Create a RW Motor Controller Board -- DONE
4. Create a MT -- Partially complete
5. Create a MT Controller Board -- DONE
6. Test, Test, Test -- Partially complete

## 2 Requirements Gathering

### A critical part of any project is gathering the correct requirements and having a design

direction. Here is a summary of the top level requirements.

### 2.1 External Constraints

- Environmental constraints and problems
- Cold welding
■ No moving parts that use metal at their interface.
- Temperature
■ Ranges from -40° to 100° C
■ Only cooling available to satellite subsystems is conduction to satellite structure. Only cooling available to entire satellite is radiative.
- Mass
■ Minimize mass, but maximize angular inertia of the RW
- Acceleration
■ Needs to be able to control acceleration with high precision.
- Mechanical System
- Size
■ Entire ACS size bounded by 4 OreSat Card slots: 40 x 90 x 90 cm ■ Each control board must be as small as possible
- Heat
■ Minimize heat output from control ICs and RWs and MTs.
■ Control card needs to be thermally sunk to the the OreSat frame.
- Electrical Power
- Supply voltage: 2.5 - 4.2 V and be capable of adapting to the range of 5.0 - 8.4 V
- Supply current: ~ 1 A continuous, with up to 3 A peak (supplied by batteries)
- Solar panels produce only 2.5 W continuously in sunlight
■ Hardware components must be capable of minimal power hibernation states in between brief periods of use.
- Attitude Control
- Reaction wheels
■ To exert strong control authority over the satellite’s orientation for brief periods of time to track a fixed point on the ground. Conserves the satellite's angular momentum.
- Magnetorquers
■ To exert very soft, 2 axis only torque against Earth's magnetic field. Changes, very slowly, the satellite's angular momentum.

- Communication
- OreSat uses a 1 Mbps Controller Area Network (CAN) serial bus for communication among all of it’s different systems. The ACS must communicate via this bus.

## 2.2 Design Paradigm

- Firmware
- ACS is a critical part of the satellite, a failure resistant design was desired.
- Real time operating systems are ideal for time critical applications, in which some guarantee of an input being acted upon within a certain time frame is needed.
- To reduce power consumption, as well as storage size, the code should be as compact and efficient as possible.

## 2.3 Maintainability

- Organizational
- OreSat is a project primarily contributed to and worked on by students. This necessitates the ability for new individuals to be able to join the project and quickly contribute meaningful work. This requires comprehensive and efficient documentations as a whole, as well as quick “bring up” guides and “onboarding” specific documentation.
- Continuation
- Portability
■ Code portability is highly desirable across all the different OreSat systems to aid fast development, efficient debugging, and allow developers to help where they are needed. To facilitate this, we try to use a single processor family and OS for as many subsystems as possible.
- Adaptability
■ Research done while developing ACS can be used for other applications of BLDC motor control.
- Maintainability
■ The ACS must be well documented in order for future engineers to catch up and contribute as fast as possible.

## 3 Results

This section is organized by the six deliverables outlined in our proposal.

## 3.1 Determined RW Motor Configuration and Placement

### Only three reaction wheels (RWs) are required to do three axis attitude control on a

satellite. However, there are some RW arrangements which provide unique advantages. See Figure 3.1.1.


### Figure 3.1.1 -- Tetrahedral and Pyramidal RW arrangements (Kök 2012, Figure 5.1)

We chose a pyramidal arrangement of reaction wheels (RWs), originally described in Logan 2008. The four RW pyramidal arrangement allows for a single RW system to fail without impacting total system functionality, as well as increased performance from smaller wheels working together. Further, the pyramidal arrangement packs better into a

flat cubic shape like found in a CubeSat.

See Figure 3.1.2 and 3.2.3 for our RW arragement.


Figure 3.1.2 - Pyramidal arrangements of Reaction Wheels

Figure 3.1.3 - Another view into the pyramidal system showing the space constraints

## 3.2 Selected and tested a RW Motor

A 2U CubeSat has such a small angular inertia that even extremely small reaction wheels (RWs) can be chosen, assuming they can reach sufficient speeds. A half dozen small DC brushless motors were chosen and tested. Figure 3.2.1 shows the D1104-4000KVA, a widely available, inexpensive, commercial off-the-shelf DC brushless motor chosen for the RWs. This particular motor has mounting holes on both sides, is compact, and it's

"outrunner" topology of magnets on the outer rotor wall increases its moment of inertia, a positive outcome for a RW.


### Figure 3.2.1 - D1104-4000KVA motor (courtesy Albert Kim, YouTube)

### For operation in the space environment, the motor's small but standard sized metal-on-metal ball bearings must be replaced with hybrid bearings, which use cermaic

balls to minimize vacuum welding and galling.

## 3.3 Create a RW Motor Controller Board

Most of the work for this project was put into the electronics control board that runs the

### RWs and MTs. Figure 3.3.1 shows the block diagram for the board, and Figure 3.3.2

shows the final results.


### Figure 3.3.1 - Block diagram of ACS control board

Figure 3.3.2 - Electronic control boards. Right two boards are "flat prototype" boards,

### middle two boards are unstuffed final design, upper left is a completed and working final

design, and lower left is a RW with 3D printed mounting bracket.

## 3.3.1 Hardware

### The following hardware was chosen:

- Microcontroller: STM32F042K6
- This is the default development chip being used in the overall OreSat Project.
- We did our initial development for this environment so we would be forced to make the bulk of the code lightweight and portable.
- No floating point unit means that our development can be used for a much broader range on MCUs
- Magnetorquer controller: STSPIN230
- Low voltage triple half-bridge bldc motor driver designed to operate with the stm32 MCU.
- Even for use with other systems, this driver has a very small footprint as well as a very wide voltage range, making it useable with both 1 cell and 2 cell battery systems.
- Brushless DC (BLDC) Motor Driver: STSPIN250
- Uses much the same structure as the STSPIN230.
- Very small footprint.
- Both systems have thermal and electrical failure modes that can be read back to the MCU.
- BLDC Motor Encoder: AS5047P
- 14 bit on-axis magnetic rotary position sensor capable of accurately determining motor position at speeds up to 28k rpm
- Communicates with the MCU using a SPI bus interface, API, Quadrature, and Synthesized UVW, allowing for a considerable range of applications.
- Extremely small form factor for encoder.
- No moving parts.
- Printed Circuit Board
- 4 layers.
- We designed multiple revisions of a custom PCB for our ACS. This board fit within space constraints identified and was compatible with the first design of motor mounts.
- The board layout has a large bare metal interface to the mounting bracket to conduct the heat generated by the control board to the OreSat frame.
- See Figure 3.3.3.


Figure 3.3.3 - Final board layout, top and bottom boards. Note detachable programming and debugging module on the side of the PCB. Also note the sections of ground plane exposed on the bottom of the board (right) for thermal contacts to the Aluminum mounting bracket.

## 3.3.2 Firmware

### The firmware was written in C using the following tools:

- ChibiOS
- Small, portable, open source real time operating system written in C that exposes low level drivers for PWM, ADC, CAN, and SPI. ChibiOS is compiled using gcc and written to a MCU via stmlink or JTAG connection and a utility such as OpenOCD.
- GNU toolchain
- OpenOCD - open on chip debugger: Used to debug and write binary images on the MCU using JTAG
- GCC- gcc-arm-none-eabi: Open source compiler for cross compiling ARM binaries on a Linux operating system.

We designed and implemented a Mealy state machine for the purpose of controlling the attitude control system. This provides a robust system where functionality can define exactly what actions are allowed in a givens state, and exactly what state transitions are allowed. When the system is powered on it begins in the initialization state where basic functionality such as interfacing with the CAN bus is activated. From this state the ACS can transition into the ready where it is possible to transition to either the reaction wheels state or, the magnetorquer state. It is important to isolate these states since pin usage is dependent on the state and the magnetorquer must share a pin with the reaction wheels. See Figure 3.3.4.


Figure 3.3.4 - This type of software architecture allows for modular design,

### making future maintenance and modification much easier

## 3.3.3 Communication over the CAN Bus

OreSat is designed to use a controller area network bus to communicate with all of it’s disparate systems. A CAN bus is favored over other other implementations because of the certainty that OreSat will operate in the electromagnetically noisy environment of space. The CAN bus is implemented using the CANopen protocol. The ACS contains two shared buffers on the bus, one for transmitting system status and one for receiving commands from the flight computer.

Multiple ACS boards can be connected to the CAN bus, being controlled via CAN commands coming from a system controller. For debugging and system design, we used laptops with USB to CAN controllers. Each system can be individually address and sent commands that only affect that specific system. Each system is able to function with the removal of another, which will allow the flight controller to detect that a particular motor or magnetorquer has gone out, and use the remaining three to compensate.

## 3.3.4 BLDC Motor Control

Due to the limitations on processing power and lack of a floating point unit, we chose to implement Sinusoidal BLDC control. Three 120 degree shifted sine waves are produced using the PWM module of the F0. These sine waves are created using PWM, by ranging the duty cycle from 0% to 100%, in a sinusoidal pattern. The system used a Look Up Table (LUT) for generating the sinusoidal PWM:

- Low processing power, and no floating point unit
- Duty cycle - Look up table vs calculation of values ■ Pros
- We don’t have a floating point unit so this is a good option
- No need to perform calculations that are expensive for the processor.
- Sine wave calculations are more flexible but slow. A lookup table is accessed via fast pointer arithmetic.
■ Cons
- The m0 only has 32k flash memory
- Less control of input waveform to the motor.

## 3.3.5 Sensors and Feedback

### The system had two main forms of feedback:

- ADC
- The microcontroller used the ADC to monitor RW and MT current consumption, using current outputs from the STSPIN2XX ICs.
- Encoder
- The AS5047P hall effect IC provides absolute motor angular position to the MCU over the SPI bus. This information is used to determine the location of the next duty cycle in the lookup table.

## 3.3.6 Reaction Wheel and Control Card Mounting System

### The PCB is attached to the BLDC motors using an innovative bracket system which holds the motor, magnet, and ACS PCB. The PCB is mounted in such a way that the ground plane is directly held against the Aluminum bracket in order to have maximum thermal

contact.


Figure 3.3.5 - New backet system on the right, show through transparent PCB

### 3.4 Create a Magnetorquer (MT)

### The magnetorquer directly changes the satellite's angular momentum by weakly torquing

against the Earth's magnetic field for long periods of time. The MTs were not fully designed
at time of our project; too much was still unknown with the power and space budgets, as well as the lack of system requirements. However, MTs are simply solenoids (coils of wire), so we use small hand wound coils to prototype the MT drivers. Future teams will specify, wind, and connect the MTs to the current ACS board.

## 3.5 Create a MT Controller Board

The Magnetorquers are driven by the STSPIN 250 IC brushed motor drivers on the ACS board. This gave us a simple and readily available method for generating the controlled current necessary to drive a magnetorquer in a small form factor with integrated thermal and electrical fault feedback. The ACS board should be able to control a wide range of

MT designs, as long as the voltage and current capabilities are followed.

## 3.6 Test, Test, Test

We demonstrated a fully operational reaction wheel (RW) system, and a full yworking magnetorquer (MT) control circuit. Tests were done to confirm rotational speed and current control. However, no time was left in the project to do environmental testing in a thermal vacuum chamber. Now that a thermal vacuum chamber has been acquired, we plan to do this testing later this summer.

## 4 Conclusion and Future Work

### The team successfully design and built a reaction wheel and magnetorquer control board for the OreSat CubeSat. Reaction wheels were fully operational, and a mock-up

magnetorquer was run.

### The team would like to thank the Oregon Space Grant Consortium's Undergraduate

Team Award Program (UTEAP) program for making this work possible.

### Finally, we've identified future work to be performed before flight:

- The STM32F042K6 limited software development because of processing power.

It also required multiplexing systems together to accommodate the number and types of output that were available. This forced us to separate the operation of the magnetorquer driver and the BLDC driver, making it ill advised to have both systems active at the same time. Therefore, we plan to upgrade to a larger, more powerful microprocessor; namely the STM32L452CE. This MCU is faster, has more pins exposed, and consumes less power than the STM32F042k6 because

of its ability to utilize multiple low power modes.

### - We intend to implement Field Oriented Control (FOC) as the next improvement to motor control, as our upgraded processor will be able to support the required processing power and now includes a floating point unit. This will allow us greater

control over the motor at high speeds, and better performance overall.
- A new bracket design was created to fit a larger RW "flywheel" in a smaller space. The final board will be re-laid out to match this form factor.

### - Extensive thermal and vacuum environmental testing, especially around the BLDC

motor bearings and heat transfer from the motor controller ICs.

## 5 References

Kök, I. (2012). Comparison and Analysis of Attitude Control Systems of a Satellite Using Reaction Wheel Actuators. Retrieved from http://www.diva-portal.org/smash/get/diva2:1020537/FULLTEXT02.pdf

Logan, J. J. (2008). Control and Sensor Development on a Four-Wheel Pyramidal Reaction Wheel Platform. Retrieved from http://digitalcommons.calpoly.edu/cgi/viewcontent.cgi?article=1032&context=theses

# 6 Final Budget

WAITING ON FINAL NUMBERS FROM PSU DEPARTMENTAL RESEARCH ADMINISTRATORS...

## A Appendix

A.1 Terms and Definitions

ADC - Analog to digital converter

CAN - Controller area network

ChibiOS - An open source RTOS

IC - Integrated circuit

JTAG - Joint Test Action Group is an industry standard for interfacing with, testing, and verifying the design of hardware.

LUT - Lookup Table

Magnetorquers - Electromagnetic coils used by a satellite system to stabilize, detumble, and barbeque roll. These coils interact with the Earth’s magnetic field to control the attitude of the satellite.

MCU - A Microcontroller unit is a small computer processor on an integrated circuit.

Mealy State Machine - A Mealy machine is a finite state machine where the output is determined by its current state and inputs.

PWM - Pulse-Width Modulation

Reaction Wheels - a system of flywheels used to adjust the attitude of a satellite.

RTOS - Real-Time Operating System

SPI - Serial peripheral interface

# Bibliography

Chibi OS: ADC Driver. (n.d.) [online] Available at: http://chibios.sourceforge.net/html/group___a_d_c.html

Chibi OS: PWM Driver. (n.d.) [online] Available at: http://chibios.sourceforge.net/html/group___p_w_m.html

Chibi OS: SPI Driver. (n.d.) [online] Available at:
http://chibios.sourceforge.net/html/group___s_p_i.html
Digikey.com. (2018). Why and How to Control Brushless DC Motors | DigiKey. [online] Available at:
https://www.digikey.com/en/articles/techzone/2017/jan/why-and-how-to-sinusoidally-contr ol-three-phase-brushless-dc-motors [Accessed 22 May 2018].
Hamblen, J. (2018). Using a Brushless DC motor with an RC ESC | Mbed. [online] Os.mbed.com.
Available at:
https://os.mbed.com/users/4180_1/notebook/using-a-dc-brushless-motor-with-an-rc-esc/[Accessed 22 May 2018].

Junquan Li, Mark Post, Thomas Wright, and Regina Lee. Design of Attitude Control Systems for CubeSat-Class Nanosatellite [online]. Journal of Control Science and Engineering, vol. 2013, Article ID 657182, 15 pages, 2013. Available at: https://www.hindawi.com/journals/jcse/2013/657182/cta/

Texas Instruments, YouTube. (2018). Brushless DC Motors & Control - How it Works (Part 1 of 2). [online] Available at: https://www.youtube.com/watch?v=ZAY5JInyHXY [Accessed 22 May 2018].

Texas Instruments, YouTube. (2018). Brushless DC Motors & Control - How it Works (Part 2 of 2). [online] Available at: https://www.youtube.com/watch?v=WyQInXjpGwU [Accessed 22 May 2018].

Vasquez, J. (2018). Anti-Cogging Algorithm Brings Out the Best in your Hobby Brushless Motors. [online] Hackaday. Available at: https://hackaday.com/2016/02/23/anti-cogging-algorithm-brings-out-the-best-in-your-hobby-brushless-motors/ [Accessed 22 May 2018].

Vedder, B. (2018). vedderb/bldc. [online] GitHub. Available at: https://github.com/vedderb/bldc [Accessed 22 May 2018].

Vedder, B. (2018). VESC – Open Source ESC | Benjamin's robotics. [online] Vedder.se. Available
at: http://vedder.se/2015/01/vesc-open-source-esc/ [Accessed 22 May 2018].

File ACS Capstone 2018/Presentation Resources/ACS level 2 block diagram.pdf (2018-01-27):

# Level 2 Block Diagram

CAN Transceiver; MCU F0; Brushed DC motor driver Full H-bridge x3; Magnetorquer x3; BLDC Motor Driver 3 half H-bridges (STSPIN230) x4; BLDC motor x4; Encoder (AS5047P) x4 CAN Input; CAN Output; PWM/6; EN/FAULT; STBY

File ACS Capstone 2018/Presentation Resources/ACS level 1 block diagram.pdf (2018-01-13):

## CAN Bus

Motor Controller Board; Motor; Board power; Motor Power

Δθ or Δθ (angular velocity or angular acceleration)

CAN Bus; Φ (Flux); Magnetorquer; Controller Board; Board Power; Magnetorquer Power

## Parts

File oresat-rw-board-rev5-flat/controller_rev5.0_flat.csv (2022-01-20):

Ref | Qnty | Value | Cmp name | Footprint | Description | Vendor
C1, C5, C7, C8, C9, C10, C11, C15, C20, C21, C22, C31, C32, C34, C35, C36, C41, C42, C46, C47, C49, C50, C53, C54, C55, C56, C57, C58, C59, C60, C61, C63, C64, C65, C66, C67, C68, C69, C70, | 39 | 100n | C_Small | Capacitor_SMD:C_0603_1608Metric | Unpolarized capacitor, small symbol
C2, C6, C18, C33, C44, C48, C51, C52, C62, C71, C72, C75, C76, C77, | 14 | 4.7u | C_Small | Capacitor_SMD:C_0603_1608Metric | Unpolarized capacitor, small symbol
C3, C4, | 2 | 20p | C_Small | Capacitor_SMD:C_0603_1608Metric | Unpolarized capacitor, small symbol
C12, C14, C19, | 3 | 1u | C_Small | Capacitor_SMD:C_0603_1608Metric | Unpolarized capacitor, small symbol
C13, C24, C25, C37, | 4 | 10n | C_Small | Capacitor_SMD:C_0603_1608Metric | Unpolarized capacitor, small symbol
C16, C17, C73, C74, | 4 | 10u | C_Small | Capacitor_SMD:C_0805_2012Metric | Unpolarized capacitor, small symbol
C23, | 1 | 47u | C_Small | Capacitor_SMD:C_0805_2012Metric | Unpolarized capacitor, small symbol
C26, C38, | 2 | 1n | C_Small | Capacitor_SMD:C_0603_1608Metric | Unpolarized capacitor, small symbol
C27, | 1 | 22n | C_Small | Capacitor_SMD:C_0603_1608Metric | Unpolarized capacitor, small symbol
C28, C39, | 2 | 100u | C_Small | project:CKG57N | Unpolarized capacitor, small symbol
C29, C30, C40, C43, C45, | 5 | 100p | C_Small | Capacitor_SMD:C_0603_1608Metric | Unpolarized capacitor, small symbol
D1, D2, | 2 | LED | LED | LED_SMD:LED_0603_1608Metric | Light emitting diode
D3, D4, | 2 | CLX6E-FKC-CH1M1D1BB7C3D3 | LED_RGB | project:LED_RGB_PLCC-6-3DMODEL | RGB LED, 6 pin package
D5, D6, D7, D8, D9, D10, D11, D12, D13, D14, D15, D16, D17, D18, D19, D20, | 16 | WS2812B | WS2812B | project:SK6812-2020 | RGB LED with integrated controller
FB1, | 1 | FerriteBead_Small | FerriteBead_Small | Inductor_SMD:L_0805_2012Metric | Ferrite bead, small symbol
H1, | 1 | RxnWheel | MountingHole | project:reaction-wheel | Mounting Hole without connection
H2, H3, H4, H5, | 4 | Mounting Hole | MountingHole | MountingHole:MountingHole_3.2mm_M3 | Mounting Hole without connection
J1, | 1 | MEZZ_PLUG | MEZZ-PLUG-IMPORT | project:MEZZANINE_PLUG
J2, | 1 | UART | Conn_01x06 | Connector_PinHeader_2.54mm:PinHeader_1x06_P2.54mm_Vertical | Generic connector, single row, 01x06, script generated (kicad-library-utils/schlib/autogen/connector/)
J3, | 1 | J-SAMTEC-TFM-120-X1-XXX-D-RA | Conn_01x40 | project:J-SAMTEC-TFM-120-X1-XXX-D-RA | Generic connector, single row, 01x40, script generated (kicad-library-utils/schlib/autogen/connector/)
J4, | 1 | PROG | Conn_02x05_Counter_Clockwise | Connector_PinHeader_1.27mm:PinHeader_2x05_P1.27mm_Vertical | Generic connector, double row, 02x05, counter clockwise pin numbering scheme (similar to DIP packge numbering), script generated (kicad-library-utils/schlib/autogen/connector/)
J5, | 1 | MEZZ_BRKOUT | Conn_01x09 | Connector_PinHeader_2.54mm:PinHeader_1x09_P2.54mm_Vertical | Generic connector, single row, 01x09, script generated (kicad-library-utils/schlib/autogen/connector/)
J6, | 1 | ADDR | Conn_02x02_Counter_Clockwise | Connector_PinHeader_2.54mm:PinHeader_2x02_P2.54mm_Vertical | Generic connector, double row, 02x02, counter clockwise pin numbering scheme (similar to DIP packge numbering), script generated (kicad-library-utils/schlib/autogen/connector/)
J7, | 1 | MOTOR | Conn_01x03 | Connector_PinHeader_2.54mm:PinHeader_1x03_P2.54mm_Vertical | Generic connector, single row, 01x03, script generated (kicad-library-utils/schlib/autogen/connector/)
J8, | 1 | DEBUG_SIG | Conn_01x10 | Connector_PinHeader_2.54mm:PinHeader_1x10_P2.54mm_Vertical | Generic connector, single row, 01x10, script generated (kicad-library-utils/schlib/autogen/connector/)
JP1, JP2, JP3, | 3 | Jumper_3_Bridged12 | Jumper_3_Bridged12 | Connector_PinHeader_2.54mm:PinHeader_1x03_P2.54mm_Vertical | Jumper, 3-pole, pins 1+2 closed/bridged
JP4, JP5, JP6, JP7, | 4 | SolderJumper_3_Bridged12 | SolderJumper_3_Bridged12 | Jumper:SolderJumper-3_P1.3mm_Bridged12_Pad1.0x1.5mm | 3-pole Solder Jumper, pins 1+2 closed/bridged
JP8, | 1 | Jumper_2_Bridged | Jumper_2_Bridged | Jumper:SolderJumper-2_P1.3mm_Bridged_Pad1.0x1.5mm | Jumper, 2-pole, closed/bridged
L1, | 1 | 6.8u | L | project:ECS-MPI4040R4 | Inductor
NT1, NT2, NT3, NT4, NT5, | 5 | NetTie_2 | NetTie_2 | NetTie:NetTie-2_SMD_Pad0.5mm | Net tie, 2 pins
R1, R6, R8, | 3 | 1k | R_Small_US | Resistor_SMD:R_0603_1608Metric | Resistor, small US symbol
R2, | 1 | 330 | R_Small_US | Resistor_SMD:R_0603_1608Metric | Resistor, small US symbol
R3, | 1 | 10k | R_Small_US | Resistor_SMD:R_0603_1608Metric | Resistor, small US symbol
R4, | 1 | 40 | R_Small_US | Resistor_SMD:R_0603_1608Metric | Resistor, small US symbol
R5, | 1 | 36.5k | R_Small_US | Resistor_SMD:R_0603_1608Metric | Resistor, small US symbol
R7, R11, | 2 | 18k | R_Small_US | Resistor_SMD:R_0603_1608Metric | Resistor, small US symbol
R9, | 1 | 47k | R_Small_US | Resistor_SMD:R_0603_1608Metric | Resistor, small US symbol
R10, | 1 | 20m | R_Shunt_US | project:WSK1206 | Shunt resistor, US symbol
R12, R13, R14, | 3 | 40m | R_Shunt_US | project:WSK1206 | Shunt resistor, US symbol
R15, | 1 | 220 | R_Small_US | Resistor_SMD:R_0603_1608Metric | Resistor, small US symbol
RN1, RN2, | 2 | 280 | R_Pack04 | Resistor_SMD:R_Array_Convex_4x0603 | 4 resistor network, parallel topology
RN3, | 1 | 36k/1% | R_Pack04 | Resistor_SMD:R_Array_Convex_4x0603 | 4 resistor network, parallel topology
RN4, | 1 | 20k/1% | R_Pack04 | Resistor_SMD:R_Array_Convex_4x0603 | 4 resistor network, parallel topology
RN5, | 1 | 4.7k | R_Pack02 | Resistor_SMD:R_Array_Convex_2x0603 | 2 resistor network, parallel topology
TP1, TP2, TP3, TP4, TP5, TP6, TP7, TP8, TP9, TP10, TP11, TP12, TP13, TP14, TP15, TP16, TP17, TP18, TP19, TP20, TP21, TP22, TP23, TP24, TP25, TP26, TP27, TP28, TP29, TP30, TP31, TP32, TP34, TP35, TP36, TP37, TP38, TP39, TP40, TP41, TP42, TP44, TP45, TP46, TP48, TP52, TP53, TP54, TP55, TP56, TP57, TP58, TP59, TP60, | 54 | TestPoint | TestPoint_Small | project:TestPoint_Keystone_5019_Minature-3DMODEL | test point
U1, | 1 | TCAN330 | TCAN330 | Package_TO_SOT_SMD:SOT-23-8 | High-Speed CAN Transceiver, 1Mbps, 3.3V supply, silent mode, shutdown mode, SOT-23-8/SOIC-8
U2, | 1 | STM32G473V | STM32G473V | Package_QFP:LQFP-100_14x14mm_P0.5mm
U3, | 1 | TPS62112 | TPS62111 | Package_DFN_QFN:QFN-16-1EP_4x4mm_P0.65mm_EP2.7x2.7mm
U4, | 1 | REF2030 | REF2030 | Package_TO_SOT_SMD:TSOT-23-5
U5, | 1 | STSPIN250 | STSPIN250 | Package_DFN_QFN:VQFN-16-1EP_3x3mm_P0.5mm_EP1.8x1.8mm
U6, U11, U12, U13, | 4 | INA185 | INA185 | Package_TO_SOT_SMD:SOT-563
U7, U8, U9, | 3 | SN74LVC1G86 | SN74LVC1G86 | Package_TO_SOT_SMD:SOT-553
U10, | 1 | STSPIN233 | STSPIN233 | Package_DFN_QFN:VQFN-16-1EP_3x3mm_P0.5mm_EP1.8x1.8mm
U14, | 1 | AS5047P | AS5047D | Package_SO:TSSOP-14_4.4x5mm_P0.65mm | On-Axis Magnetic Position Sensor, 14-bit, PWM Output, ABI Output, UVW Output, SPI Interface, TSSOP-14
U15, | 1 | MIC5504-3.3YM5 | MIC5504-3.3YM5 | Package_TO_SOT_SMD:SOT-23-5 | 300mA Low-dropout Voltage Regulator, Vout 3.3V, Vin up to 5.5V, SOT-23
Y1, | 1 | 16MHz | Crystal_GND24 | Crystal:Crystal_SMD_3225-4Pin_3.2x2.5mm | Four pin crystal, GND on pins 2 and 4

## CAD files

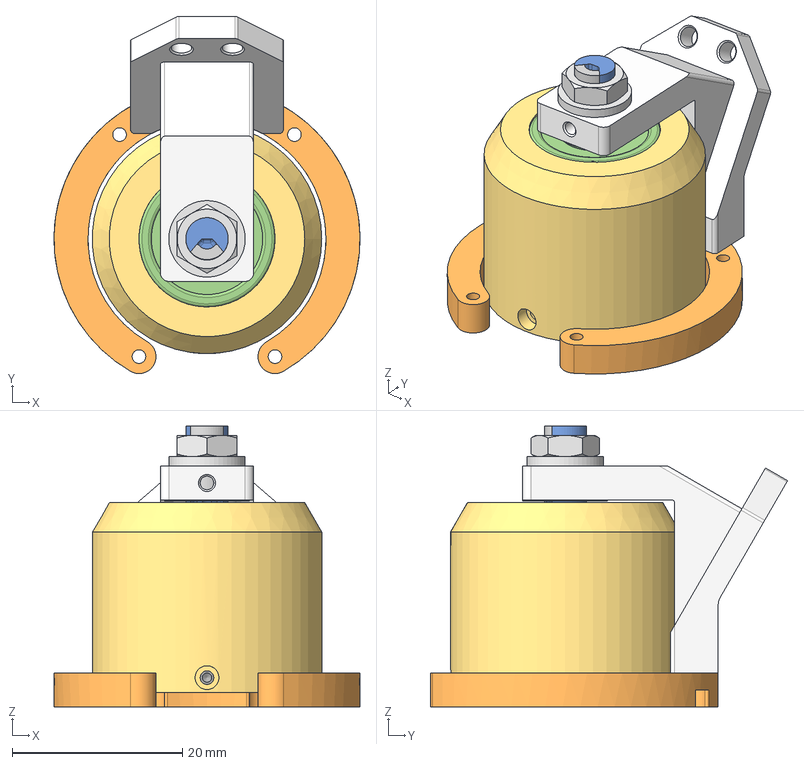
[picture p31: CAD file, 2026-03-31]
oresat-rw-board-rev2-MCXN/power-stage-rev8/3dmodels/RW Module Sub-assembly(1).step
36.0 x 42.0 x 33.1 mm

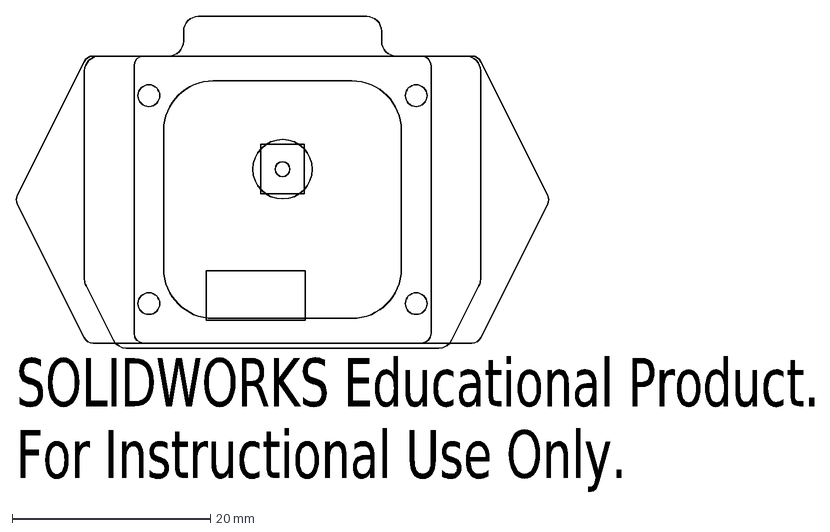
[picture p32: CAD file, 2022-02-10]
documentation/OreSat_EncoderBoard.DXF
SOLIDWORKS Educational Product.
For Instructional Use Only.

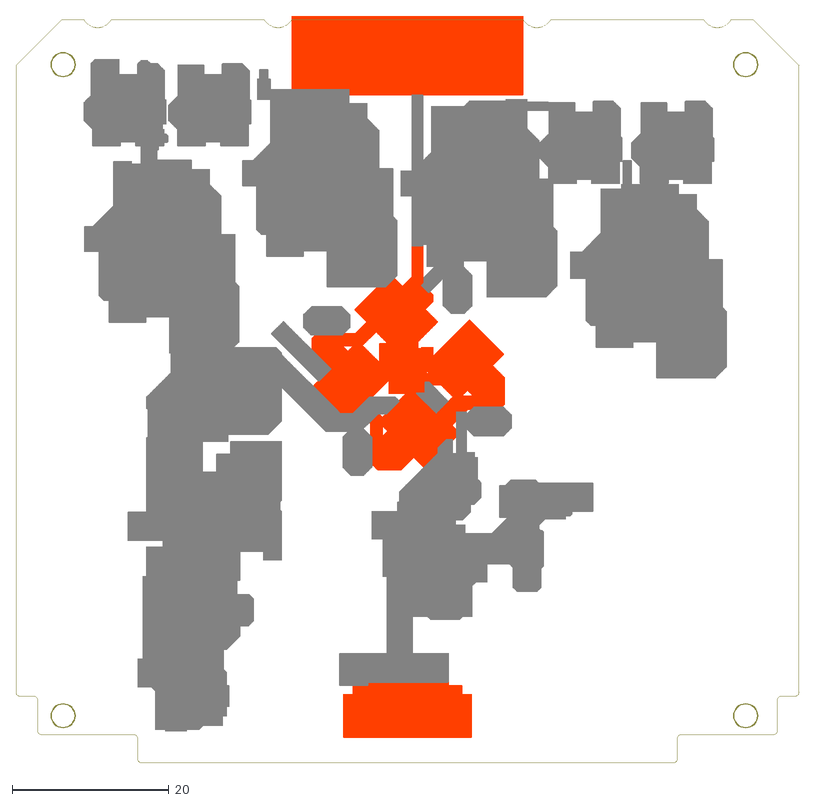
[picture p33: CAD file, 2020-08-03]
eaglecad/Mechanical References/oresat-acs-card-rev1-keepout.dxf
99.8 x 95.2

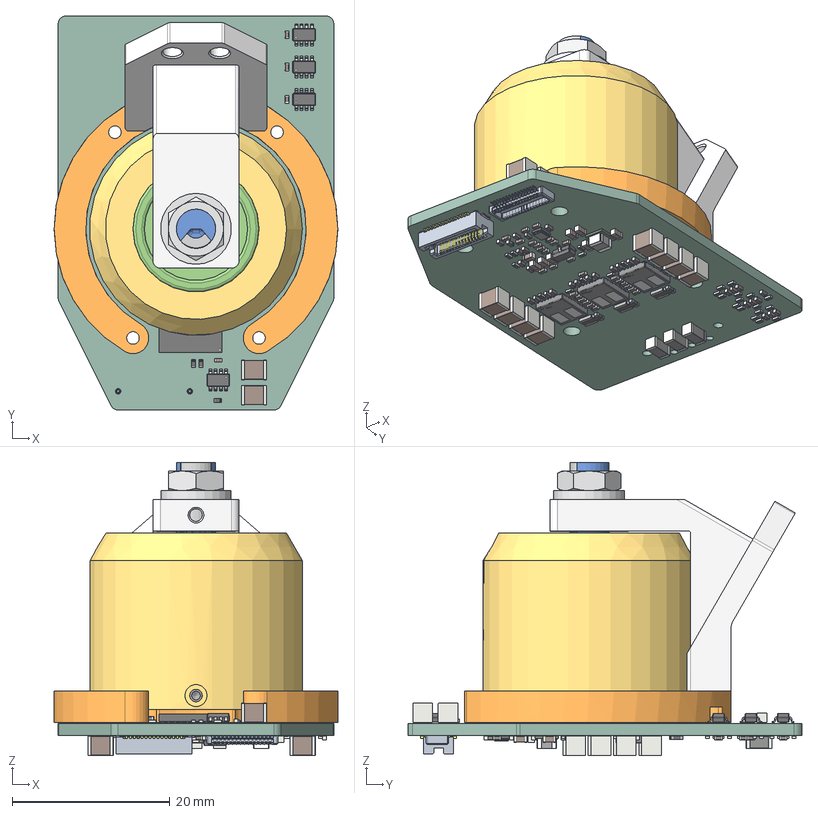
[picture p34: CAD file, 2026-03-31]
oresat-rw-board-rev2-MCXN/power-stage-rev8/power-stage-rev8-RC2.step
36.0 x 50.0 x 37.2 mm
C_0402_1005Metric x 92
L_0402_1005Metric x 6
C_0603_1608Metric x 23
R_0402_1005Metric x 46
C_0805_2012Metric x 3
SOT-23-8 x 4
R_0805_2012Metric x 3
SOLDERMASK-BTM-SIL0010D
SUBSTRATE-SIP x 2
SOLDERMASK-TOP
INDUCTOR-BODY
INDUCTOR-TERMNL x 2
C_1210_3225Metric x 10
power-stage-rev8-RC2 1.52.1
Axle Connection
Axle
RW
TFBGA-100_8x8mm_Layout10x10_P0.8mm
QFN-16-1EP_3x3mm_P0.5mm_EP1.7x1.7mm
Crystal_SMD_2520-4Pin_2.5x2.0mm
Texas Logo Yury x 3
L_1206_3216Metric x 3
SOT-23
R_Shunt_Vishay_WSKW0612 x 3
SOLDERMASK-SIS0011A
METAL-SIS0011A
INDUCTOR-BODY-MLV
INDUCTOR-TERMNL-MLV x 2
10132797-031100LF
power-stage-rev8_PCB

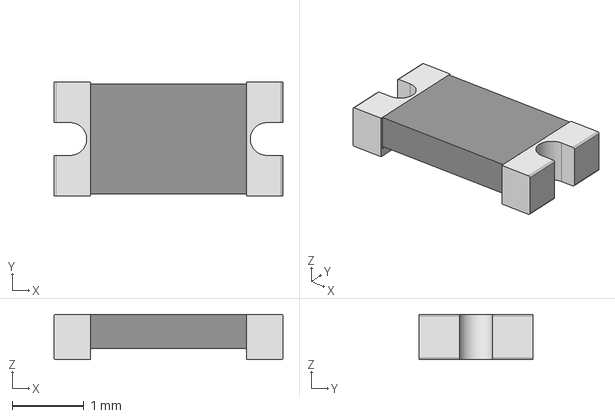
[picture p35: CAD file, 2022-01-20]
oresat-rw-board-rev5-flat/3dmodels/WSK1206.stp
3.20 x 1.60 x 0.635 mm

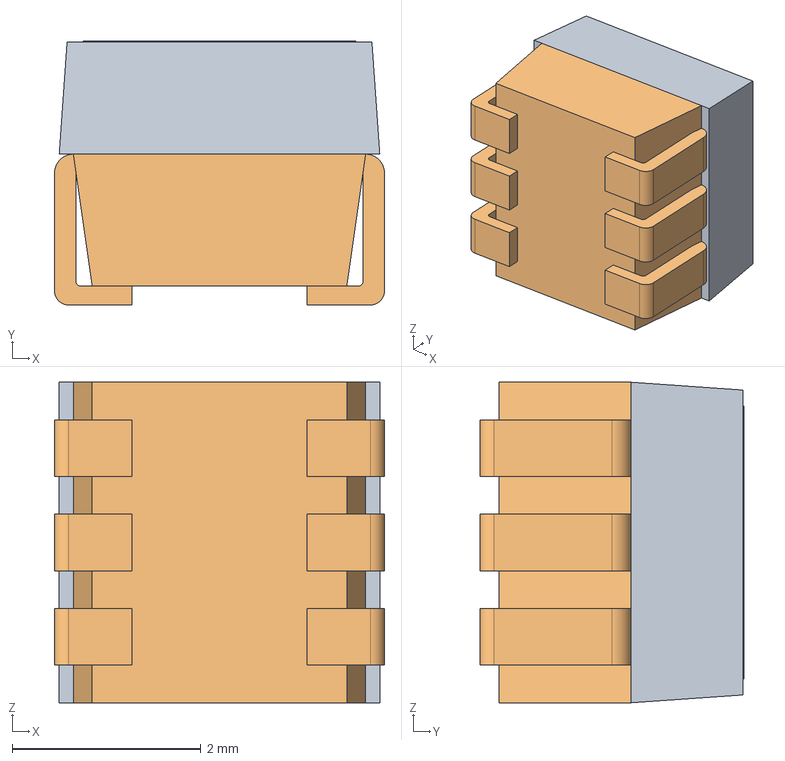
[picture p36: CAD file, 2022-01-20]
oresat-rw-board-rev5-flat/Cree_PLCC6.stp
3.50 x 2.80 x 3.40 mm
CORPS-DPLACER_COPI0001_1
CORPS-DPLACER_COPI0002_1

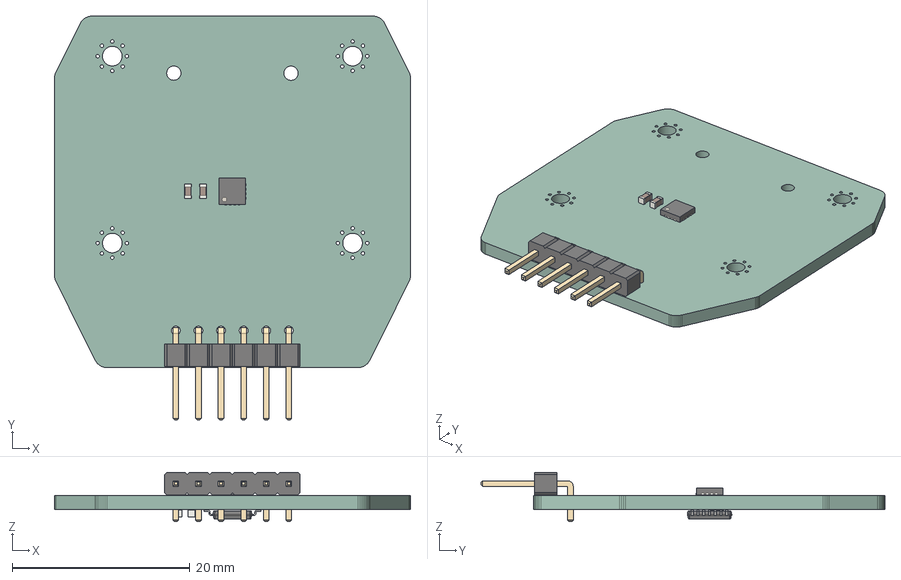
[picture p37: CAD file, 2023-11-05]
oresat-rw-board-rev7/as5047p_breakout_rev2/as5047p_breakout_rev2.step
40.0 x 45.4 x 5.54 mm
as5047p_breakout_rev2 PCB

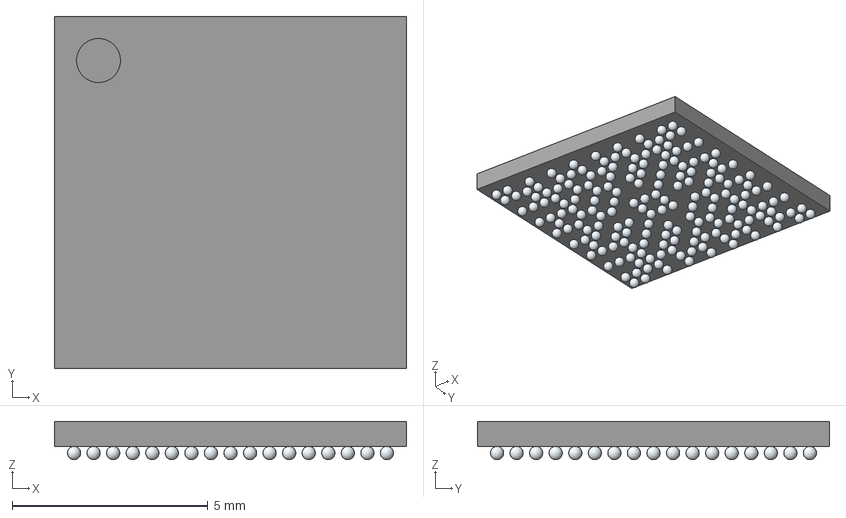
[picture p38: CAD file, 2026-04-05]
oresat-rw-board-rev2-MCXN/power-stage-rev8/3dmodels/MCXN947VDFT.stp
9.00 x 9.00 x 0.98 mm
A1
A2
A4
A6
A8
A10
A12
A14
A16
A17
B1
B2
B3
B4
B6
B7
B8
B10
B11
B12
B14
B15
B16
B17
C3
C4
C5
C6
C8
C9
C10
C12
C13
C14
C15
D1
D2
D3
D4
D6
D7
D9
D11
D12
D14
D15
D16
D17
E4
E5
E7
E8
E10
E11
E13
E14
F1
F2
F3
F4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

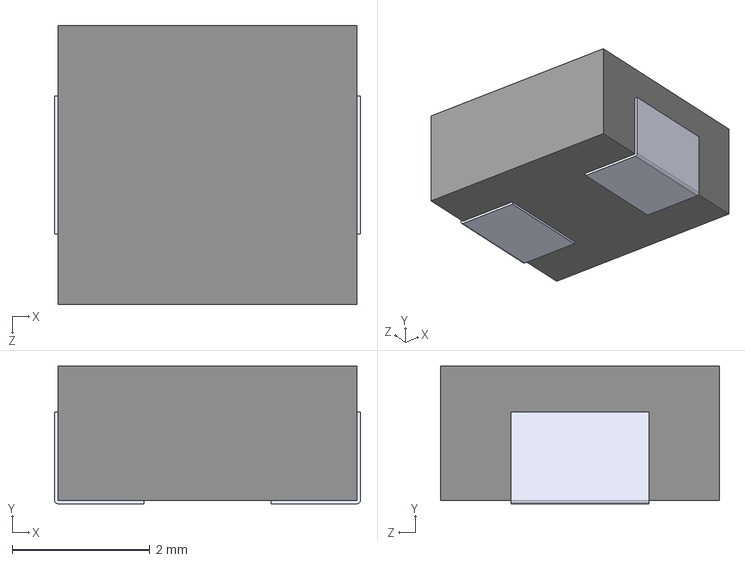
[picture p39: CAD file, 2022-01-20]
oresat-rw-board-rev5-flat/3dmodels/ECS-MPI4040R4-6R8-R.step
4.45 x 2.00 x 4.06 mm

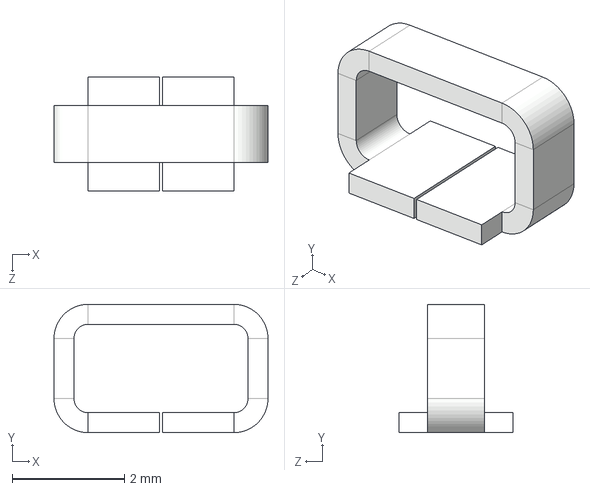
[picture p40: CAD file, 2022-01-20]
oresat-rw-board-rev5-flat/keystone-PN5019.STEP
3.81 x 2.29 x 2.03 mm

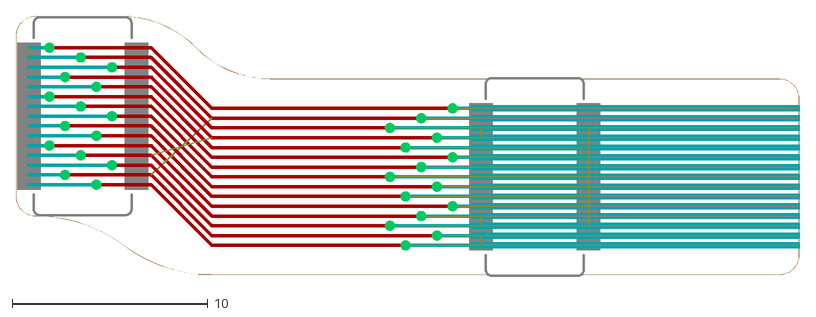
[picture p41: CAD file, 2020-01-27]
eaglecad/Mechanical References/connector_cable.dxf
40.1 x 13.3

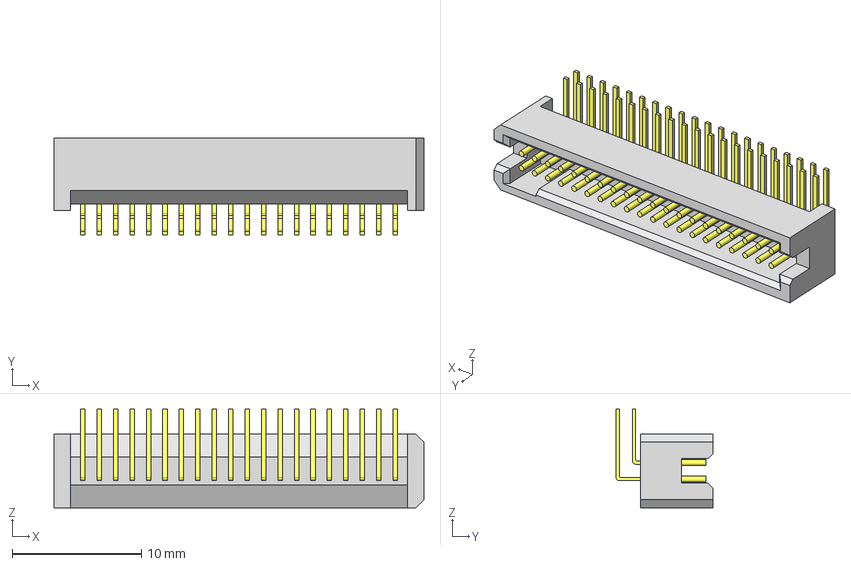
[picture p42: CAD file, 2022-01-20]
oresat-rw-board-rev5-flat/3dmodels/TFM-120-01-L-D-RA.stp
28.6 x 7.49 x 7.62 mm
_TFM-120-01-L-D-RA_terminal
_TFM-120-01-L-D-RA_pins

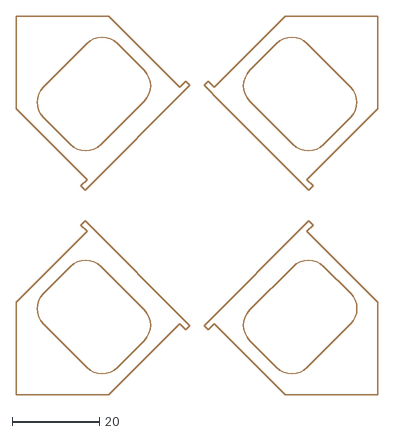
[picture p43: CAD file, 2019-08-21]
eaglecad/Mechanical References/rw_cage.dxf
83.0 x 86.8

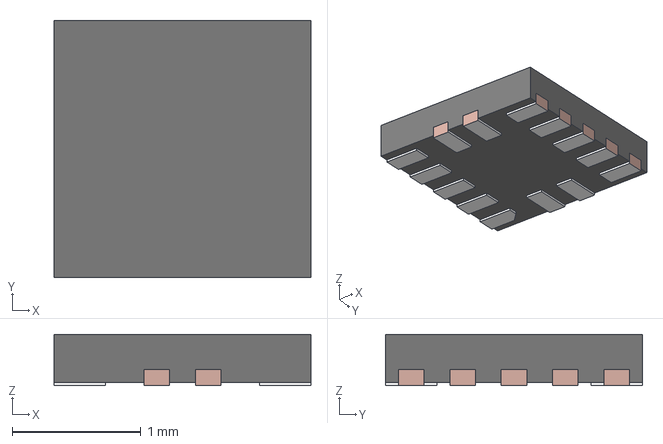
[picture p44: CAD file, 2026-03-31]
oresat-rw-board-rev2-MCXN/power-stage-rev8/3dmodels/RUC0014A.stp
2.00 x 2.00 x 0.4 mm
FRAME

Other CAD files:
eaglecad/Mechanical References/controller_rev4.2b.dxf
oresat-rw-board-rev5-flat/3dmodels/WS2812-2020.step
oresat-rw-board-rev2-MCXN/power-stage-rev8/3dmodels/IC_LMG2100R044_VQFN-FCRLF16.STEP
oresat-rw-board-rev2-MCXN/power-stage-rev8/3dmodels/arm.stp
oresat-rw-board-rev2-MCXN/power-stage-rev8/3dmodels/10132797-021100LF.stp
oresat-rw-board-rev2-MCXN/power-stage-rev8/3dmodels/10132797-031100LF.stp
oresat-rw-board-rev2-MCXN/power-stage-rev8/3dmodels/10132798-021100LF.stp
oresat-rw-board-rev2-MCXN/power-stage-rev8/3dmodels/10132798-031100lf.stp
oresat-rw-board-rev2-MCXN/power-stage-rev8/3dmodels/436500315.stp
oresat-rw-board-rev2-MCXN/power-stage-rev8/3dmodels/547220304.stp
oresat-rw-board-rev2-MCXN/power-stage-rev8/3dmodels/555600307.stp
oresat-rw-board-rev2-MCXN/power-stage-rev8/3dmodels/94669A094_Aluminum Unthreaded Spacer.STEP
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

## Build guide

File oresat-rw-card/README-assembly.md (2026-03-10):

# OreSat Reaction Wheel (RW) Card

# Description

The OreSat RW Card is a 99.8 x 94.6 x 1.6 mm four layer PCB with a mix of 
through-hole and SMT components on the top and bottom sides.

# Printed Circuit Board Assembly (PCBA) Information

## Assembly info

- Assemble to IPC Class 2 or better
- Bake components that are not moisture sealed to appropriate levels as required.
- Solder paste MUST be leaded.
- Aqueous flux and wash strongly preferred.
   - Clean to NASA Standard "Visibly Clean (VC)": No particles or residues are visible to the naked eye.
- No conformal coating.
- Ship in antistatic protective bag

## Component Specific Assembly Information

N/A

## Assembly Files

### Bill of materials

| Filename | Description |
| --- | --- |
| -bom.csv | BOM in Comma Separated Variable format |

### Mounting location files

| Filename | Description |
| --- | --- |
| -3u.pos | Pick and place locations for components |

### Stencils

| Filename | Notes |
| --- | --- |
| -B_Paste.gbr | RS274X file for solder paste stencil |
| -F_Paste.gbr | RS274X file for solder paste stencil |

### Other Assembly Information

| Filename | Description |
| --- | --- |
| -ipc2581.xml | IPC-2581 netlist and board layout file  |

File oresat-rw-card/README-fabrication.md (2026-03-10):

# OreSat Reaction Wheel (RW) Card

# Description

The OreSat RW Card is a 99.8 x 94.6 x 1.6 mm four layer PCB with a mix of 
through-hole and SMT components on the top and bottom sides.

# Printed Circuit Board (PCB) Fabrication information

- 4 layer board
   - Board thickness is 1.59 mm (0.063 inch) +/- 2 mil)
   - Bounding box is 99.8 x 94.6 mm
- Design Rules
    - Minimum Trace / Space design rules
       - Outer layers: 0.127 mm (5.0 mil) / 0.127 mm (5.0 mil)
       - Inner layers: 0.127 mm (5.0 mil) / 0.127 mm (5.0 mil)
    - Outer dimension router tolerance: +/- 0.254 mm (10.0 mil)
    - Hole placement tolerance: +/- 0.075 mm (3.0 mil)
    - Inner tab routed slot tolerance: +/- 0.254 mm (10.0 mil)
- Drills
   - Drill Positional Tolerance: 0.051 mm (2.0 mil)
   - Drill Size tolerance: +/- 0.064 mm (2.5 mil)
- Plated/Un-plated holes
  - There are 2 un-plated (NPT) holes
  - There are 629 plated through (PTH) holes
  - PTH minimum diameter: 0.254 mm (10 mil)
  - PTH minimum annulus: 0.102 mm (4 mil) radius
- Slots
  - There is 1 interior unplated slots
- There are 6 fiducials
   - 3 on the top layer
   - 3 on the bottom layer
- Panel tabs
   - No requirements, besides try to minimize board protrusions
- If not otherwise specified, build to IPC 6012 Class 2 or better.

## Materials

- Outside copper layers is 1 oz Cu after plating (0.043 mm / 1.7 mil)
- Inside copper layers are 0.5 oz Cu (0.018 mm / 0.7 mil)
- There are no requirements on the prepreg or core of this four layer stackup.
- Board Surface treatment should be ENIG, althogh immersion Silver is acceptable.
- White silkscreen on top and bottom surface
- Taiyo PSR-4000 or equivalent soldermask on top and bottom

## Array / Panel Information

- Coordinate with Contract Manufacturer (CM) for optimal size of this panel.
- If no feedback from CM, then produce single boards (no panel).

## Fabrication Files in "fabrication" Folder

### PCB Artwork

| Filename | Notes |
| ---| --- |
| -Edge_Cuts.gbr | RS274X file for the dimension (outline) layer |
| -F_Silkscreen.gbr | RS274X file for the top silkscreen |
| -F_Mask.gbr | RS274X file for the top soldermask |
| -F_Cu.gbr | RS274X file for the top copper layer |
| -In1_Cu.gbr | RS274X file for the layer 2 copper |
| -In2_Cu.gbr | RS274X file for the layer 3 copper |
| -B_Cu.gbr | RS274X file for the bottom copper layer |
| -B_Mask.gbr | RS274X file for the bottom soldermask |
| -B_Silkscreen.gbr | RS274X file for the bottom silkscreen |
| -NPTH.drl | Excellon file for non-plated through holes |
| -PTH.drl | Excellon file for plated through holes | 

### Other Fabrication Information

| Filename | Notes |
| --- | --- |
| -ipc2581.xml | IPC-2581 board information file |

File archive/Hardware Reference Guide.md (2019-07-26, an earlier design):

# Hardware Reference Guide:
This includes a description of the purpose for each component by name as listed on the Rev 4 schematic. It also covers decisions about pin wiring desisions for some of the more complex chips and why certain choices were made.

## Micro Controller
* U100: STM32L452CEU3- STM micro controller runing an M4 core with low power periphrials. The 52CEU3 was chosen because of its low pin count, small footprint, and higher operating temperature range along with meeting all other requiered specifications.
  * pin 1: VBAT - This pin allows for minimal processes to be kept running from a button cell battery and opperates as a battery charging output when lower than VDD. It is tied to VDD so the charge circuitry will remain inactive and so that the low power oscilator function is never activated
  * pin 36: VUSB- This pin provieds power to the internal USB peripherials. Since this board isn't programmed over usb, it is better to tie this pin low to ensure the usb peripherials don't use power. 
  * pins 3 and 4: Low power oscillator input- left disconnected. VBAT being greater than VDD activates the system that opperates from this clock input and since VBAT is tied to VDD, those systems are never activated.
* C101-C102: Decoupling capacitors for VDD
* C103: Decoupling capacitor for VDDA
* C104-C105: Clock Capacitor
* C106: This capacitor prevents parasitic reset
* R101: Boot pull down resistor
* X101: ABM10-16MHz Crystal Oscillator

### CAN Transceiver 
* U101: TCAN330- Ti CAN transceiver for CAN communication
* C107: Decoupling capacitor

## Voltage Regulator
* U200: TPS63070- Ti Boost Buck Converter. Selected to maintain similarity to other oresat systems
  * pin 2: Power Good output- not connected to save space
  * pin 5: Voltage output set- Biased by R204 and R205 to set output at 3.3V (pg.17)
  * pin 6: Voltage scaler for the feedback pin- not connected because only one output voltage is needed
* C201-C203: Current buffer/ magnetic decoupling for VBUS
* C204: Provides capacitence to the internal voltage regulator
* C205-206: Current buffer/ magnetic decoupling for 3.3V output
* L201: Inductor for internal voltage regulator
* R201: Pull up resistor for Enable and PS/Sync, This turns on the regulator, and allows it to run using Pulse Frequency Modulation (PFM) as a power saving measure
* R202: No Place - Allows for expanded functionallity such as syncing the PWM/PFM to an external clock to control noise frequency
* R203: Pull down resistor for VSEL to hold FB2 (pin6) low
* R204-R205: Provides biased voltage feedback for 3.3V output based on the relationship R204/R205 = Vout/Vref - 1

## Reaction Wheel Driver
* U300: STSPIN230- STM brushless motor driver. This was chosen because of its exceptionally small footprint and periphrial options, as well as a wide voltage range
* C301-C303: Current buffer/ magnetic decoupling from VBUS
* C304: Filter cap for STBY/RESET pin
* C305: Filter cap for EN/FAULT pin
* R301: Pullup Resistor for STBY/RESET
* R302: Isolates EN from FAULT feedback so that if the driver goes into fault, the enable pin on the MCU can still be high while allowing the fault pin to be pulled to ground
* JP301: 2mm header pin- Connects to the reaction wheel leads. Located near one of the arms of the motor cage so the wires can be wrapped

### Current Feedback
* U301: TSV991ILT- OpAmp for current feedback from the motor driver to the micro controller. This particular OpAmp was selected because of its use in the development board used to prototype the STSPIN230
* C306-C307: Current buffer/ magnetic decoupling from 3.3V
* C308: Input filter
* C309: Output filter
* R303-R304: DC bias for input voltage
* R305-R306: Current shunt for the driver output. These resistors handle the current load running through the reaction wheel. If current feed back is not necisary, ground pins 4 and 9 on the driver
* R307-R308: Feedback gain control. If the gain needs to be altered, it is prefered to modify R308 over R307 due to the filtering in the feedback path

### Motor Encoder:
* U302: AS5047P- 14-bit on axis magnetic rotery position sensor with 12-bit binary incremantal pulse count for high speed capability. This part was chosen for so many reasons. It doesn't have any moving parts making it space ready. It is capable of maintaining an accurate reading of possition even at high speeds. It has high accuracy output of position over SPI enabling phase vector control of the reaction wheels. It also boasts quadrachure encoding output, which is very useful for mechanical characterization of the motor and any weights attatched to it (these measurements are very important for running the motor more efficiently and using less power). This part is why the circuit boards are oriented perpendicularly to the moter, its possition relative to the motor axel is very important. It is also capable of simulating a hall effect sensor set up... just 'cause.
  * pin 4: MOSI- You may have noticed that there is a data pin tied high. The MOSI pin controles which mode the AS5047 chip is in. As it turnes out, the mode we want it in is activated by the signal 0xffff. So in effect, tying it high sends the signal 0xffff
* C310: Decouping cap
* R309: Pull up resistor to set MOSI to 0xffff

## Magnetorquer Driver
* U400: STSPIN250- STM brushed motor driver. This was chosen because of its similarities to the STSPIN230 and runs about the same parameters that are needed for the magnetorquers in a very small footprint with a wide voltage input range.
  * pins 15 and 16 are connected to ground as specified in the datasheet (pg.10)
* C401-C403: Current buffer/ magnetic decoupling from VBUS
* C404-C406: filter caps
* C407: Timing cap for internal oscilator
* R401: Pull up resistor
* R402: Isolates EN from FAULT feedback so that if the driver goes into fault, the enable pin on the MCU can still be high while allowing the fault pin to be pulled to ground
* R403-R404: Current limiting resistors
* R405-R406: Voltage bias circuit
* R407-R408: Timing resistors for internal oscillator

### Current Feedback
* U401: TSV991ILT- OpAmp for current feedback from the motor driver to the micro controller. This particular OpAmp was selected because of its use in the development board used to prototype the STSPIN250
* C408-C409: Current buffer/ magnetic decoupling from 3.3V
* C410: Input filter
* C411: Output filter
* R409-R410: DC bias for input voltage
* R411-R412: Current shunt for the driver output. These resistors handle the current load running through the reaction wheel. If current feed back is not necisary, ground pins 4 and 9 on the driver
* R413-R414: Feedback gain control. If the gain needs to be altered, it is prefered to modify R414 over R413 due to the filtering in the feedback path

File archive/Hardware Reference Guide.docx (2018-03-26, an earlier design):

# Hardware Reference Guide

# Voltage Regulator

R208: Current limiting resistor to protect the LED from burning.

D201: LED light to indicate that battery power is connected.

R201: Jumper resistor.

C201, C202, C203: Bypass capacitors for filtering high frequency spikes in voltage.

R202: Pull-up resistor to pull PS/SYNC up to VBAT voltage.

R203: NP resistor. A place-holder in case PS/SYNC needs to be pulled down to GND.

TP201, TP202, TP203, TP205: Test points for probing voltage.

C204: Filter capacitor.

R204: Pull-down resistor.

L201: Main inductor for buck-boost topology. The inductor allows the voltage to be boosted.

U200: 2-V to 16-V Buck-Boost Converter With 3.6-A Switch Current for stepping battery voltage down to a stable 3.3 volts.

R205, R206: Voltage divider.

R207: NP resistor in case we need a pull-up resistor here.

C205, C206, C207: Bypass capacitors for filtering high frequency spikes in voltage.

R209: Current limiting resistor to protect the LED from burning.

D202: LED light to indicate that 3.3V is active.

# CAN Transceiver

JP101: A 1x4 pinheader for connecting jumper wires.

U101: CAN transceiver chip for CAN communication.

C106: Filtering capacitor.

# Microcontroller Unit - STM32F0

JP102: Special pin connector for USART communication.

C101, C102, C103: Filtering capacitors.

U100: Microcontroller (MCU) for controlling pretty much everything else.

TP101: Test point for probing voltage.

R101: Pull-down resistor.

X101: Crystal oscillator providing a reference frequency for the microcontroller.

C104, C105: Filtering capacitors.

J1: Connector for both JTAG and SWD programming. This allows us to write and rewrite code to the microcontroller.

# BLDC motor driver IC (STSPIN230)

R301: Pull-up resistor.

C304: Filter capacitor?

R302: This resistor partially isolates the EN input from the FAULT output. If the MCU is driving EN high but the STSPIN230 IC pulls FAULT low then the R302 resistor will act as a 18k path to GND so that the MCU is not shorted to GND.

C305: Filter capacitor?

U300: The STSPIN230 is a motor driver IC for driving the BLDC motor.

R303: Jumper resistor to connect to the battery power rail.

R304: NP resistor to serve as a placeholder in case we want to jumper to the 3.3V rail instead of the batter power rail. This will most likely not be necessary. We are quite confident that we will be driving the motor with the direct battery power. But it is nice to have this option for our first prototype.

C301, C302, C303: Large capacitor bank for filtering high frequency voltage spikes and providing power when instantaneous current draw is needed.

JP301: A 1x3 pinheader for connecting the BLDC motor.

R305, R306, R307: Current limiting resistors to protect the LEDs from burning.

LEDU, LEDV, LEDW: LED lights so that we can visually see the commutation sequence of the motor driver. Basically, these LEDs allow a sanity check so we can see if our commutation pattern is actually occurring.

# Current feedback from BLDC driver

R314: Jumper resistor. We can remove this if we want to isolate things.

U301: An operational amplifier IC configured in a non-inverting amplifier configuration.

C307: Filtering capacitor. This capacitor allows high frequencies through the feedback loop thus reducing the gain at high frequencies.

R313, R312: These resistors set the feedback bias and thus set the gain of the amplifier.

C308, C309: Filtering capacitors.

C306: Filtering capacitor shorts high frequencies to GND.

R308, R309: Voltage divider capacitors bias the voltage level of the IN+ node on the op amp.

R310, R311: These small resistors take the large amount of current going through the motor and a small voltage drop is produced across them. If more current flows through the motor then the voltage drop across the resistors increases. This in turn increases the voltage bias at the IN+ node of the op amp. The op amp takes that voltage level and amplifies it. The amplified voltage is seen at the OUT node of the op amp. Thus, the amount of current through the motors converts to a voltage level seen at the OUT pin of the op amp.

# Encoder:

R315: Pull-up resistor.

C310: Filtering capacitor.

U302: The AS5047P encoder IC gives us position information so we know the orientation of the motor. The motor shaft has a magnet connected to its drive shaft. The encoder IC sits close to the magnet and uses an internal array of Hall-effect sensors to determine the orientation of the motor shaft.

JP302: Pinheader to connect to quadrature output. This will not be needed for flight but it is useful for characterizing the motor.

# Magnetorquer driver IC (STSPIN250)

R401: Pull-up resistor.

C404, C405: Filtering capacitor.

R402: This resistor partially isolates the EN input from the FAULT output. If the MCU is driving EN high but the STSPIN250 IC pulls FAULT low then the R402 resistor will act as a 18k path to GND so that the MCU is not shorted to GND.

R409, R410: Voltage divider biases the ‘REF’ pin to a desired voltage. The is voltage level is compared to the voltage on the sense pin. When V_(SENSE) >V_(REF) the current limiter is triggered and the IC temporarily goes into a protective state.

R408: This resistor determines the length of the protective state, the “OFF time”.

R407, C406: RC network in parallel with R408 helps to stabilize the off timer circuitry.

C407: Filtering capacitor.

U400: The STSPIN250 is a motor driver IC for driving brushed DC motors. The Magnetorquer is essentially a large inductor just like a brushed DC motor is essentially just a large inductor.

R403: Jumper resistor to connect to the battery power rail.

R404: NP resistor to serve as a placeholder in case we want to jumper to the 3.3V rail instead of the batter power rail. This will most likely not be necessary. We are quite confident that we will be driving the motor with the direct battery power. But it is nice to have this option for our first prototype.

C401, C402, C403: Large capacitor bank for filtering high frequency voltage spikes and providing power when instantaneous current draw is needed.

JP401: Pinheader for connecting the Magnetorquer.

R411, R412: Current limiting resistors to protect the LEDs from burning.

LED+, LED-: LED lights so that we can visually see if we are sending current through the Magnetorquer.

# Current feedback from Magnetorquer driver

R419: Jumper resistor. We can remove this if we want to isolate things.

U401: An operational amplifier IC configured in a non-inverting amplifier configuration.

C411: Filtering capacitor. This capacitor allows high frequencies through the feedback loop thus reducing the gain at high frequencies.

R418, R417: These resistors set the feedback bias and thus set the gain of the amplifier.

C409, C410: Filtering capacitors.

C408: Filtering capacitor shorts high frequencies to GND.

R413, R14: Voltage divider capacitors bias the voltage level of the IN+ node on the op amp.

R415, R516: These small resistors take the large amount of current going through the Magnetorquer and a small voltage drop is produced across them. If more current flows through the Magnetorquer then the voltage drop across the resistors increases. This in turn increases the voltage bias at the IN+ node of the op amp. The op amp takes that voltage level and amplifies it. The amplified voltage is seen at the OUT node of the op amp. Thus, the amount of current through the Magnetorquer converts to a voltage level seen at the OUT pin of the op amp.

Nathaniel Dusciuc ACS Capstone 2/10/18

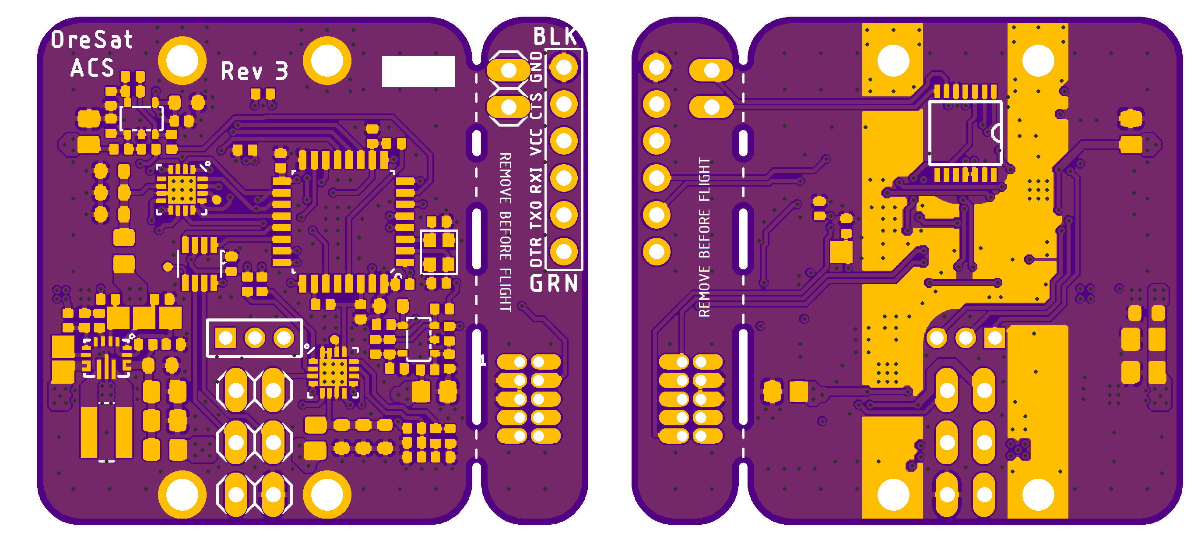
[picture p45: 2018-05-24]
ACS Capstone 2018/Presentation Resources/Manufacturing photos/Poster Print.png

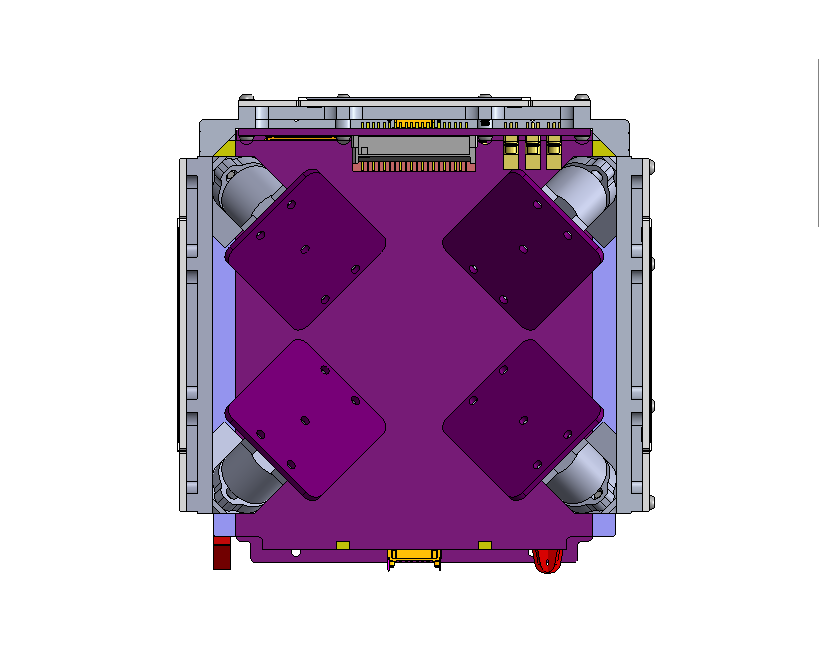
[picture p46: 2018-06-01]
ACS Capstone 2018/Presentation Resources/Manufacturing photos/CAD model of mounting in frame (5).png

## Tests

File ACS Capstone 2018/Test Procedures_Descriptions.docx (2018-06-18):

Test Case | 1.0
Test Type | Functional/Hardware
Test Name | Power-On
Test Purpose | Bring-up the power regulator circuitry safely and check verify that the board is receiving 3.3v correctly.
Tools Required | 1. DC power supply (with current limiting functionality). 2. Multimeter.
Steps Required | 1. Set DC power supply to 4.2v and limited to 100mA. 2. Connect DC power supply to VBAT and GND planes on the board. 3. Connect multimeter to measure voltage on the 3.3v plane. 4. Turn on the output of the DC power supply and observe the current output. If the current is maxing out at 100mA there may be a short or a badly placed IC. 5. Observe the voltage reading from the DC power supply. It should close to 3.3v.
Test Result (P/F) | Pass! Yay!
Observations? | First attempt was a fail. The power regulator output was ~0v. We resoldered the regulator IC and tried again. Second attempt was a fail. The power regulator was outputting 4.56v. We found the issue. The voltage divider circuit was telling the IC to output 4.56v. The voltage divider was using a 470kohm and 100kohm resistor. We changed the voltage divider to 470kohms and 150kohms. Third attempt was a success! We observed ~40mA being drawn from the DC power supply. This is well within a safe region and indicates that we do not have any shorting.

Test Case | 2.0
Test Type | Functional/Unit
Test Name | CAN
Test Purpose | Purpose of the test is to confirm that we can receive correct data over CAN
Tools Required | 3. CAN client software required to send CAN messages from laptop to transceiver. 4. Minicom needs to be installed for serial output.
SW document name | app_test_CAN
Steps Required | 6. Build and load app_test_CAN code to the microcontroller. 7. Send CAN message from client SW to transceiver. 8. Print sent message on serial monitor using minicom. 9. Message on the serial monitor should be the same message sent from CAN client software.
Test Result (P/F)
Observations?

Test Case | 2.1
Test Type | Functional/Unit
Test Name | DC motor test.
Test Purpose | Spin DC motor without current feedback.
Tools | 1. ARM toolchain. 2. OpenOCD
SW document name | app_test_brushed
Steps Required | 1. Build and load app_test_brushed code to the microcontroller. 2. Motor should be spinning. a. Confirm that the motor can speed up and down. b. Confirm the motor can switch directions.
Test Result (P/F) | PASS
Observations? | 1. The motor spins both directions and changes speed. 2. There is an error in the Rev1 flat-sat board layout. There is no connection between the 0ohm and NP resistors on the N$20 net. We had to create a solder bridge here so that the Vs pin on the STSPIN250 can receive VBATT.

Test Case | 2.1.0
Test Type | Functional/Integration
Test Name | DC Current Control
Test Purpose | Spin DC motor with current feedback.
Tools | 1. ARM toolchain. 2. OpenOCD. 3. Minicom
SW document name | app_test_brushed_adc
Steps Required | 1. Make sure the serial connections are in place. 2. Build and load app_test_brushed_adc code to the microcontroller. 3. Motor should be spinning moments after loading code. a. Confirm that the ADC is reading expected current value. b. (add info for exact value expected)
Test Result (P/F)
Observations?

Test Case | 2.2
Test Type | Functional/Unit
Test Name | Read encoder output.
Test Purpose | Observe the encoder is providing correct output from corrected angle register.
Tools | 1. ARM toolchain. 2. OpenOCD. 3. Minicom
SW document name | app_test_encoder
Steps Required | 1. Make sure the serial connections are in place. 2. Build and load app_test_encoder code to the microcontroller. 3. Spin the motor manually and observe that the output ranges from 0 to 16383.
Test Result (P/F) | PASS
Observations? | 1. Reacts to a magnet consistently.

Test Case | 2.3
Test Type | Functional/Unit
Test Name | BLDC Motor Test
Test Purpose | Observe the bldc motor spins via brute force method.
Tools | 1. ARM toolchain. 2. OpenOCD.
SW document name | app_test_bldc
Steps Required | 1. Build and load app_test_bldc code to the microcontroller. 2. The motor must be spinning moments after the mcu is flashed.
Test Result (P/F) | PASS
Observations? | 1. Functions as expected.

Test Case | 2.3.0
Test Type | Functional/Integration
Test Name | BLDC Current control test
Test Purpose | Observe ADC output while bldc motor is spinning.
Tools | 1. ARM toolchain 2. OpenOCD 3. Minicom
SW document name | app_test_bldc_adc
Steps Required | 1. Make sure the serial connections are in place. 2. Build and load app_test_bldc_adc code to the microcontroller. 3. The motor must be spinning moments after the mcu is flashed. 4. Observe the ADC output through minicom.
Test Result (P/F)
Observations?

Test Case | 2.4
Test Type | Integration
Test Name | BLDC Integration
Test Purpose | Spin the motor using encoder feedback while ADC provides voltage.
Tools | 1. ARM toolchain 2. OpenOCD 3. Minicom
SW document name | app_test_bldc_integrated
Steps Required | 1. Make sure the serial connections are in place. 2. Build and load app_test_bldc_integrated code to the microcontroller. 3. The motor must be spinning moments after the mcu is flashed. 4. Observe that the output ranges from 0 to 16383. 5. Observe output from the ADC
Test Result (P/F) | PASS
Observations? | 1. Encoder feedback works with motor.

Test Case | 2.5
Test Type | Integration
Test Name | System test
Test Purpose | Ensure the entire system functions.
Tools | 1. ARM toolchain 2. OpenOCD 3. Minicom
SW document name | app_test_acs
Steps Required | 1. Make sure the serial connections are in place. 2. Build and load app_test_acs code to the microcontroller. 3. Send CAN message to activate BLDC motor. a. The motor must be spinning b. Observe that the output ranges from 0 to 16383. c. Observe output from the ADC 4. Send CAN message to shutdown BLDC motor. a. The motor must stop spinning. 5. Send CAN message to start DC motor. a. DC motor must be spinning. b. Observe ADC is reading voltage.
Test Result (P/F)
Observations?

ACS Capstone Team 5/4/2018

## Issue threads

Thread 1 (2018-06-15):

Driver Standby/Reset Pins

NathanDus, 2018-06-15:
The STBY/RESET pins on both the STSPIN230 and STSIN250 need to be reverted back to rev1.1

E-Ruhl, 2018-06-17:
We also need to look into weather it would be better to alternate the enable pin off the MCU or if we get lower power usage by dissabling the Standby pin instead of the enable pin.

E-Ruhl, 2019-06-29:
Stepping up to the L4 allowed us to put both pins on GPIO

Closed 2019-06-29.

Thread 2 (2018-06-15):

Delete 'Board Schematic PDFs' folder

NathanDus, 2018-06-15:
Hi Eric, I don't know how to cleanly remove things from Git. It doesn't like it when I try. Can you delete the folder 'Board Schematic PDFs'? Its not needed anymore. We have things in the 'Board Schematic PDFs and Images' folder.

heliochronix, 2018-06-15:
@NathanDus,
To remove something from Git, use `git rm`. It acts pretty much like regular `rm` but also stages the changes inside git. For example, in the oresat-acs-board directory you would do `git rm -r Board\ Schematic\ PDFs`. Hope that helps!

heliochronix, 2018-06-15:
Also, then you would `git commit` the changes. Note that empty directories are automatically removed from git repositories if there's nothing inside.

Closed 2018-06-17.

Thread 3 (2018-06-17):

Gain on Current Feedback OpAmps

E-Ruhl, 2018-06-17:
We need to look into what kind of feedback we want for the ADC. At the moment it has a gain of 1 and has an offset around 10% or so of VCC.

andrewgreenberg, 2022-10-11:
REv 4.1 deprecated.

Closed 2022-10-11.

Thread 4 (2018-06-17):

OreSat Standard Card Mount

E-Ruhl, 2018-06-17:
This needs to be developed in parallel with the ACS driver board mounts so that the connections can easily be made between the boards and the card

Joedang, 2018-06-22:
I don't think the ACS driver board will have any effect on the card mounting per se. I still think it's a good idea to have a flexible connection between the  ACS driver boards and the card. That wouldn't mess with the way the card goes into the structure. At any rate, we should meet at some point to play with the CAD and figure out a good form factor for the Rev4 driver board.

E-Ruhl, 2019-06-29:
Currently looking into FFC connections. Potential problem with mechanically fastening them. Will talk with Patrick about potentially modifying cage to operate as a clamp.

andrewgreenberg, 2022-10-11:
This is fixed in ADCS >= v1.2 and upcoming RW rev 7.

Closed 2022-10-11.

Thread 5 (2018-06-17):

Board Mounts

E-Ruhl, 2018-06-17:
The layout of Rev3 needs to be altered so it takes up less of a verticle footprint as well as making a solid connection to the Standard OreSat Card. Redesign should be done in parallel with Rev4 layout so there is more of a process than with rev3.

E-Ruhl, 2019-06-29:
Rev4 cage mounts have a shorter profile.

Closed 2019-06-29.

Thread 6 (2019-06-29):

Programmer adapter board feedback

E-Ruhl, 2019-06-29:
There is potential to add feedback LEDs on the adapter board to show data flow and power. Is this something that would be useful?

E-Ruhl, 2019-07-29:
LEDs added

E-Ruhl, 2019-07-29:
LEDs added

Closed 2019-07-29.

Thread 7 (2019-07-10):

Power Isolation

E-Ruhl, 2019-07-10:
In the datasheet for the buck boost converter, there is an isolation gap between power and ground. This is easy enough to do, and is a good idea. Will implement in rev 4.1. increase isolation on layer 2 and layer 15.

E-Ruhl, 2019-07-29:
Added a bit more isolation

E-Ruhl, 2019-07-29:
Added a bit more isolation

Closed 2019-07-29.

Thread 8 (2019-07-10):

CAN transceiver

E-Ruhl, 2019-07-10:
Determine if the resistors are necessary in the CAN SILENT line

E-Ruhl, 2019-07-10:
Compare to CAN transceiver setup on other boards to determine if CAN BUS lines are set up properly

E-Ruhl, 2019-07-10:
Everything is fine

Closed 2019-07-10.

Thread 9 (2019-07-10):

Rev4 connectors

E-Ruhl, 2019-07-10:
Looking into different styles of connectors, I found this one:

data sheet:
https://www.hirose.com/product/document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

digikey:
https://www.digikey.com/product-detail/en/hirose-electric-co-ltd/FH34SRJ-14S-0.5SH-99/H124721CT-ND/5156024

In terms of cable, this looks pretty good:

https://www.digikey.com/product-detail/en/molex/0151660141/WM11330-ND/3281022

but we might have to peel off the shielding on one end to get the double contact from the port, also not really sure what length to get since I don't have anything for an oresat card yet. I should probably talk to Patrick about getting geometry for the board.

andrewgreenberg, 2022-10-11:
Fixed in upcoming Rev 7.

Closed 2022-10-11.

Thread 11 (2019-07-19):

Determine power draw of full system opperation

E-Ruhl, 2019-07-19:
Determine how much power the system needs and how much we're allowed to draw from the OreSat Bus.

Determine if there is enough of a power budget to run magnetorquers and Reaction wheels to run at the same time.

andrewgreenberg, 2022-10-11:
See Issues #28.

Closed 2022-10-11.

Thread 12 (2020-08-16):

ACS Card Rev 1 Bus buffer pull ups

cesarordaz, 2020-08-16:
ACS Card missing pull up resistors on magnetometer side of I2C bus buffer.
Rev 1

cesarordaz, 2020-09-12:
Fixed on new board files, but needs to be modded in to existing card

Closed 2021-04-08.

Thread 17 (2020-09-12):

Unpack OPD / Fix tNames

davidalay, 2020-09-12:
The 4x OPD is packed super tight and should probably be spaced out a bit when we move to 0603.  There is plenty of room and it is not sensitive circuit.  It just makes assembly so much easier and requires significantly less rework.  tNames layer should also be fixed when we do this.

Closed 2020-09-21.

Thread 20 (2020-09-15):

Reaction Wheel Ecnoder Boards Need Enlarged Through Hole

haydenreinhold, 2020-09-15:
Switching shoulder screws to https://www.mcmaster.com/90263A111/, meaning that the through holes will need to be slightly increased to allow room for the new 3mm wide shoulder diameter.

andrewgreenberg, 2022-10-11:
No longer relevant.

Closed 2022-10-11.

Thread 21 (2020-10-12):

C406 on Flat ACS is wrong footprint

davidalay, 2020-10-12:

andrewgreenberg, 2022-10-11:
Flat ACS no longer relevant; closing

Closed 2022-10-11.

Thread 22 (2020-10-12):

C303 C403 on flat ACS is the wrong footprint

davidalay, 2020-10-12:

andrewgreenberg, 2022-10-11:
Flat ACS is deprecated.

Closed 2022-10-11.

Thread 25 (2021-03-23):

M0 should monitor "POUT_Q"  from it's own OPD and the other 4 OPDs

andrewgreenberg, 2021-03-23:
We forgot to connect these...

andrewgreenberg, 2021-04-08:
Already monitors it's own; still needs the other four.

cesarordaz, 2023-02-05:
Not enough ADC pins to monitor POUT for all 5 OPDs. Also discovered that the M0's OPD POUT is not going into an ADC pin, just a regular GPIO pin.

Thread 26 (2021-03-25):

ACS card I2C clock and data lines need test points

tedhavelka, 2021-03-25:
2021-03-25 - ACS card I2C clock and data lines, PB6/SCL/7.4B and PB7/SDA/7.4B need test points in a location that's easier and safe to solder after board is fully populated.

Closed 2021-04-08.

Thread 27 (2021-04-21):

I2C resistors should be 4.7k

andrewgreenberg, 2021-04-21:

andrewgreenberg, 2022-10-11:
Fixed in v1.2

Closed 2022-10-11.

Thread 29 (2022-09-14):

ADCS Card MT sense filtering

cesarordaz, 2022-09-14:
Add low pass filters to the INA185 outputs on the ADCS card for the magnetorquer current sensing

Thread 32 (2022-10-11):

Change `MT_STBY/RST` to `MT_STBY_RST` (or vice versa)

andrewgreenberg, 2022-10-11:
There are two incompatible net names on the STSPIN250  `STBY/RST` lines: `MT_STBY/RST` and `MT_STBY_RST`. Probably want the former since it's the pin name?

Closed 2023-02-05.

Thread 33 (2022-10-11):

Change MT PWM outputs to be on pins with a single timer that isn't being used.

andrewgreenberg, 2022-10-11:
Dave would like to switch the MT_[XYZ]_PWM signals to PB13/PB14/PB15 so that the PWMs use an unused timer peripheral on the M0. You can switch all of the other pins around as necessary.

Closed 2023-02-05.

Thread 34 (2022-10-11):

ADCS KiCAD / EAGLE cleanup

andrewgreenberg, 2022-10-11:
There's a lot broken on the ADCS card v1.2. In vaguely priority order:

- ERC
   - Fix all of the missing libraries and footprints. For example, the card outline and connectors.
   - Ignore all of the repeated warnings
   - Once the ERC errors are cleaned up, re-import the schematic changes into the board and see what breaks.
   - There are lots of EAGLE footprints floating around, especially of resistors and capacitors. Can we switch over to the KiCAD footprints, or are they too large and thus do we need to create our own custom footprint library with the A-C designations like we had in EAGLE?
- Misc
   - Fix the global symbols to be in/out/bidirectional as necessary. Specifically, see the global labels by the microcontroller.

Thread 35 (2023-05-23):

Need soft start on the RW OPDs

andrewgreenberg, 2023-05-23:
Apparently the RWs have like 200 uF of distributed capacitance, so we're going to need to charge that at a sane rate. So let's add soft start to the main CB switch. This is probably a good thing, because we shouldn't be hard starting anything really on the satellite.

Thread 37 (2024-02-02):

Add slow start to Card OPD

andrewgreenberg, 2024-02-02:
The 66 uF worth of caps on the magnetorquer drivers browns out the C3 card when the ADCS card is powered on. Add a slow start to the Q26.

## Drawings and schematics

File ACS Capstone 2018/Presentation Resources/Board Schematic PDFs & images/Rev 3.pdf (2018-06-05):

## 3.3V SPS

A

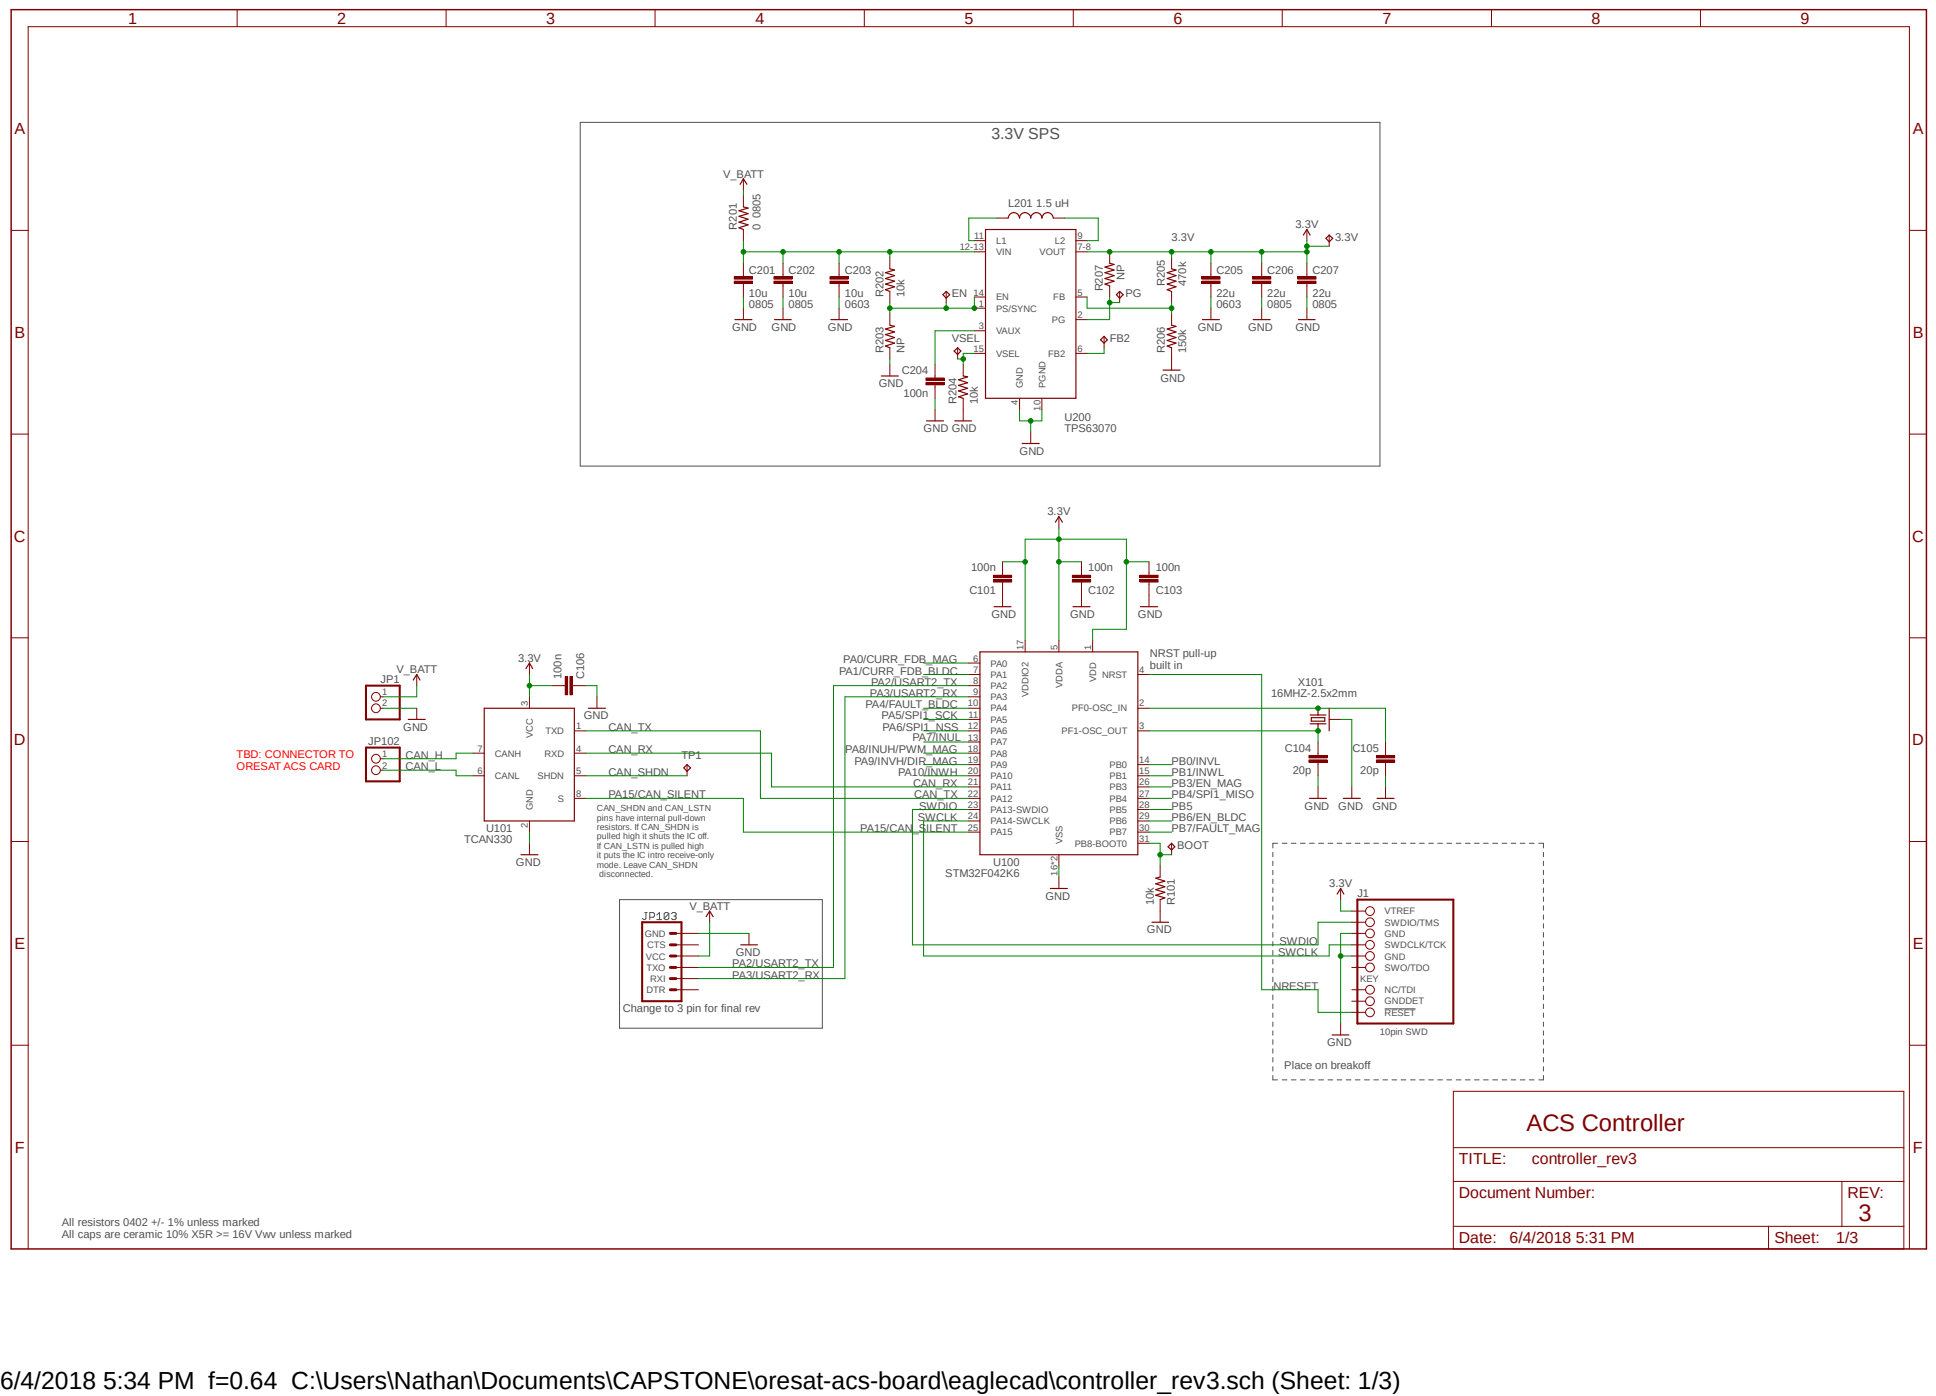
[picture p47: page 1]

TBD: CONNECTOR TO ORESAT ACS CARD

SWCLK CAN_RX CAN_RX
CAN_SHDN and CAN_LSTN
pins have internal pull-down
resistors. If CAN_SHDN is pulled high it shuts the IC off.

PB7/FAULT_MAG
NC/TDI GNDDET RESET BOOT

If CAN_LSTN is pulled high
it puts the IC intro receive-only mode. Leave CAN_SHDN

Document Number: | REV: 3

All resistors 0402 +/- 1% unless marked All caps are ceramic 10% X5R >= 16V Vwv unless marked

Date: 6/4/2018 5:31 PM | Sheet: 1/3

6/4/2018 5:34 PM f=0.64 C:\Users\Nathan\Documents\CAPSTONE\oresat-acs-board\eaglecad\controller_rev3.sch (Sheet: 1/3)

A

A

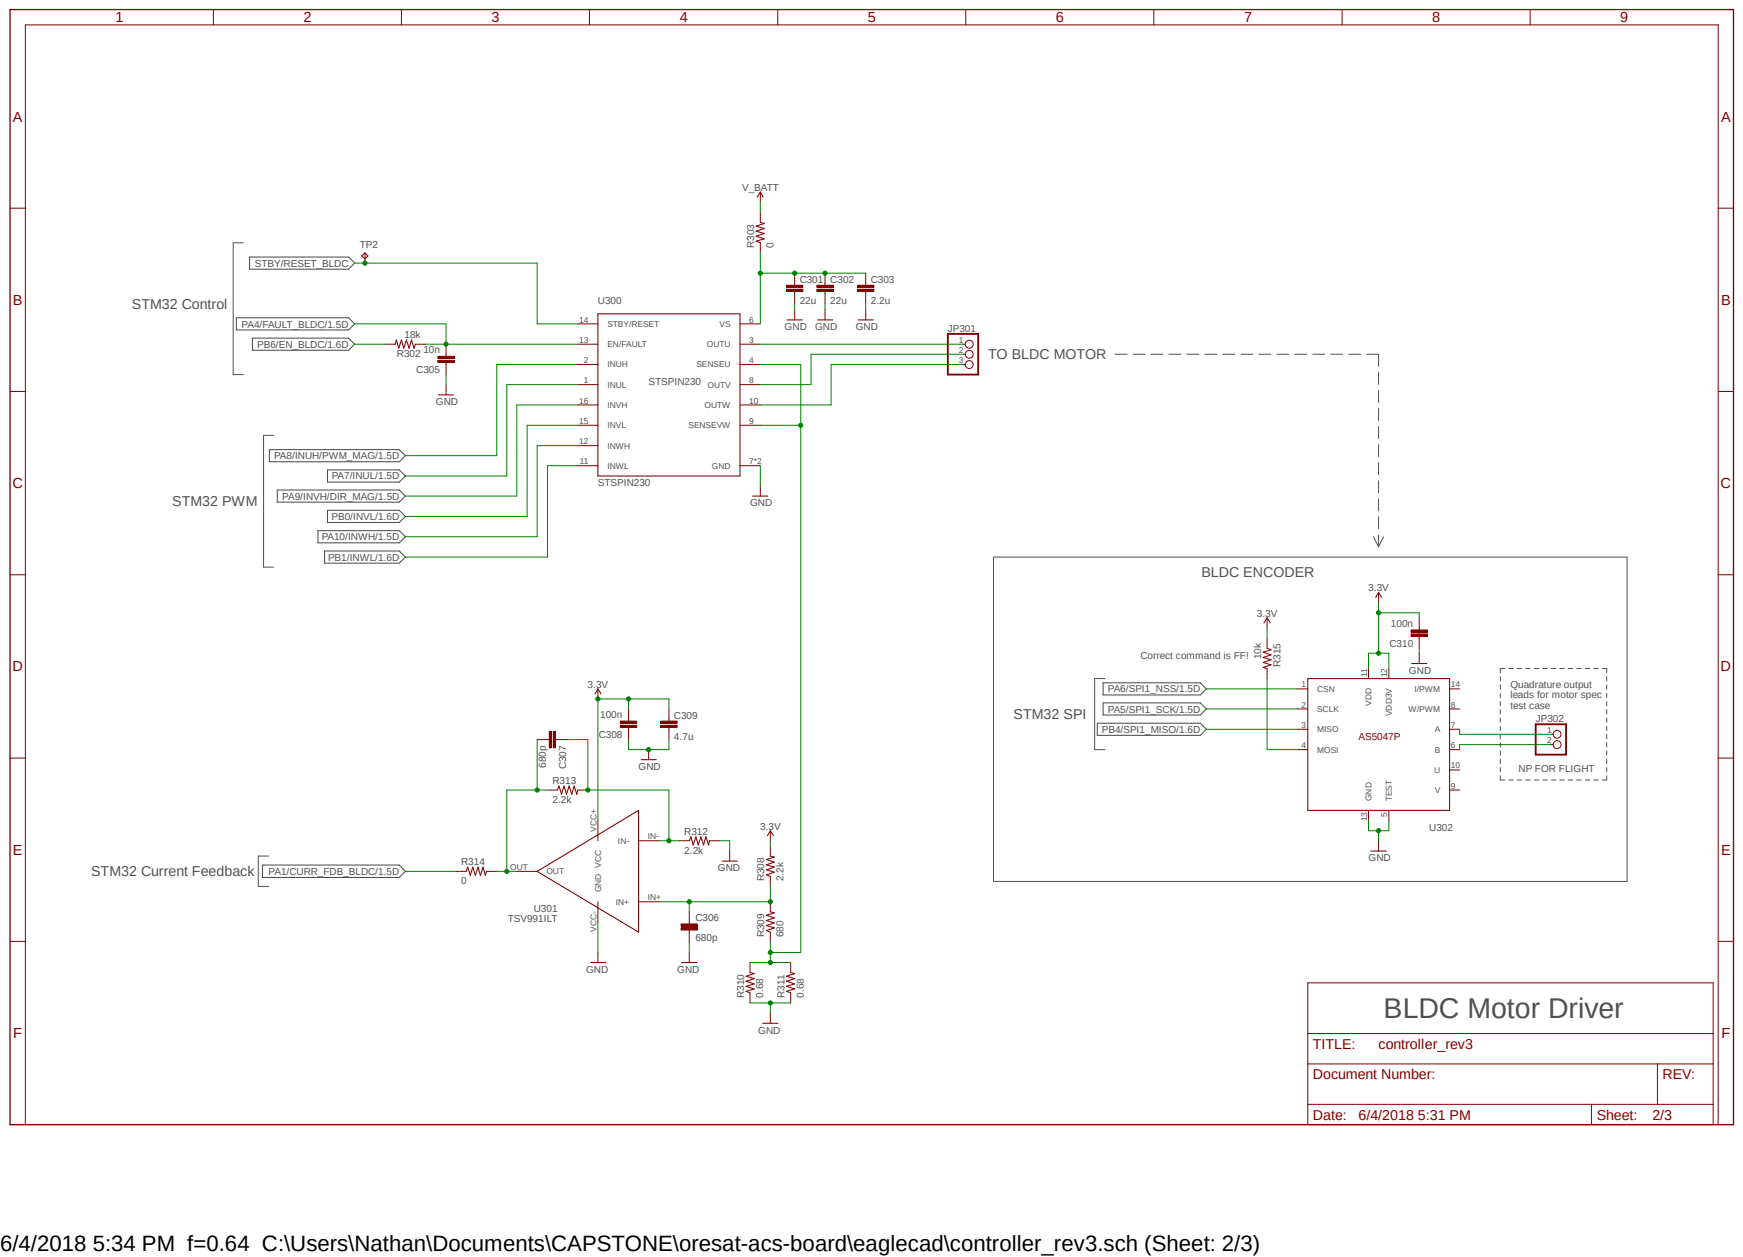
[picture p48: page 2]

leads for motor spec
test case NP FOR FLIGHT

Document Number: | REV:

Date: 6/4/2018 5:31 PM | Sheet: 2/3

6/4/2018 5:34 PM f=0.64 C:\Users\Nathan\Documents\CAPSTONE\oresat-acs-board\eaglecad\controller_rev3.sch (Sheet: 2/3)

R402 | R405 R406 R⁴⁰⁷ | R⁴⁰⁸ R⁴⁰⁹ R⁴¹⁰ R418 R419 | R417 | R⁴¹³ R⁴¹⁴ | R⁴⁰³

A

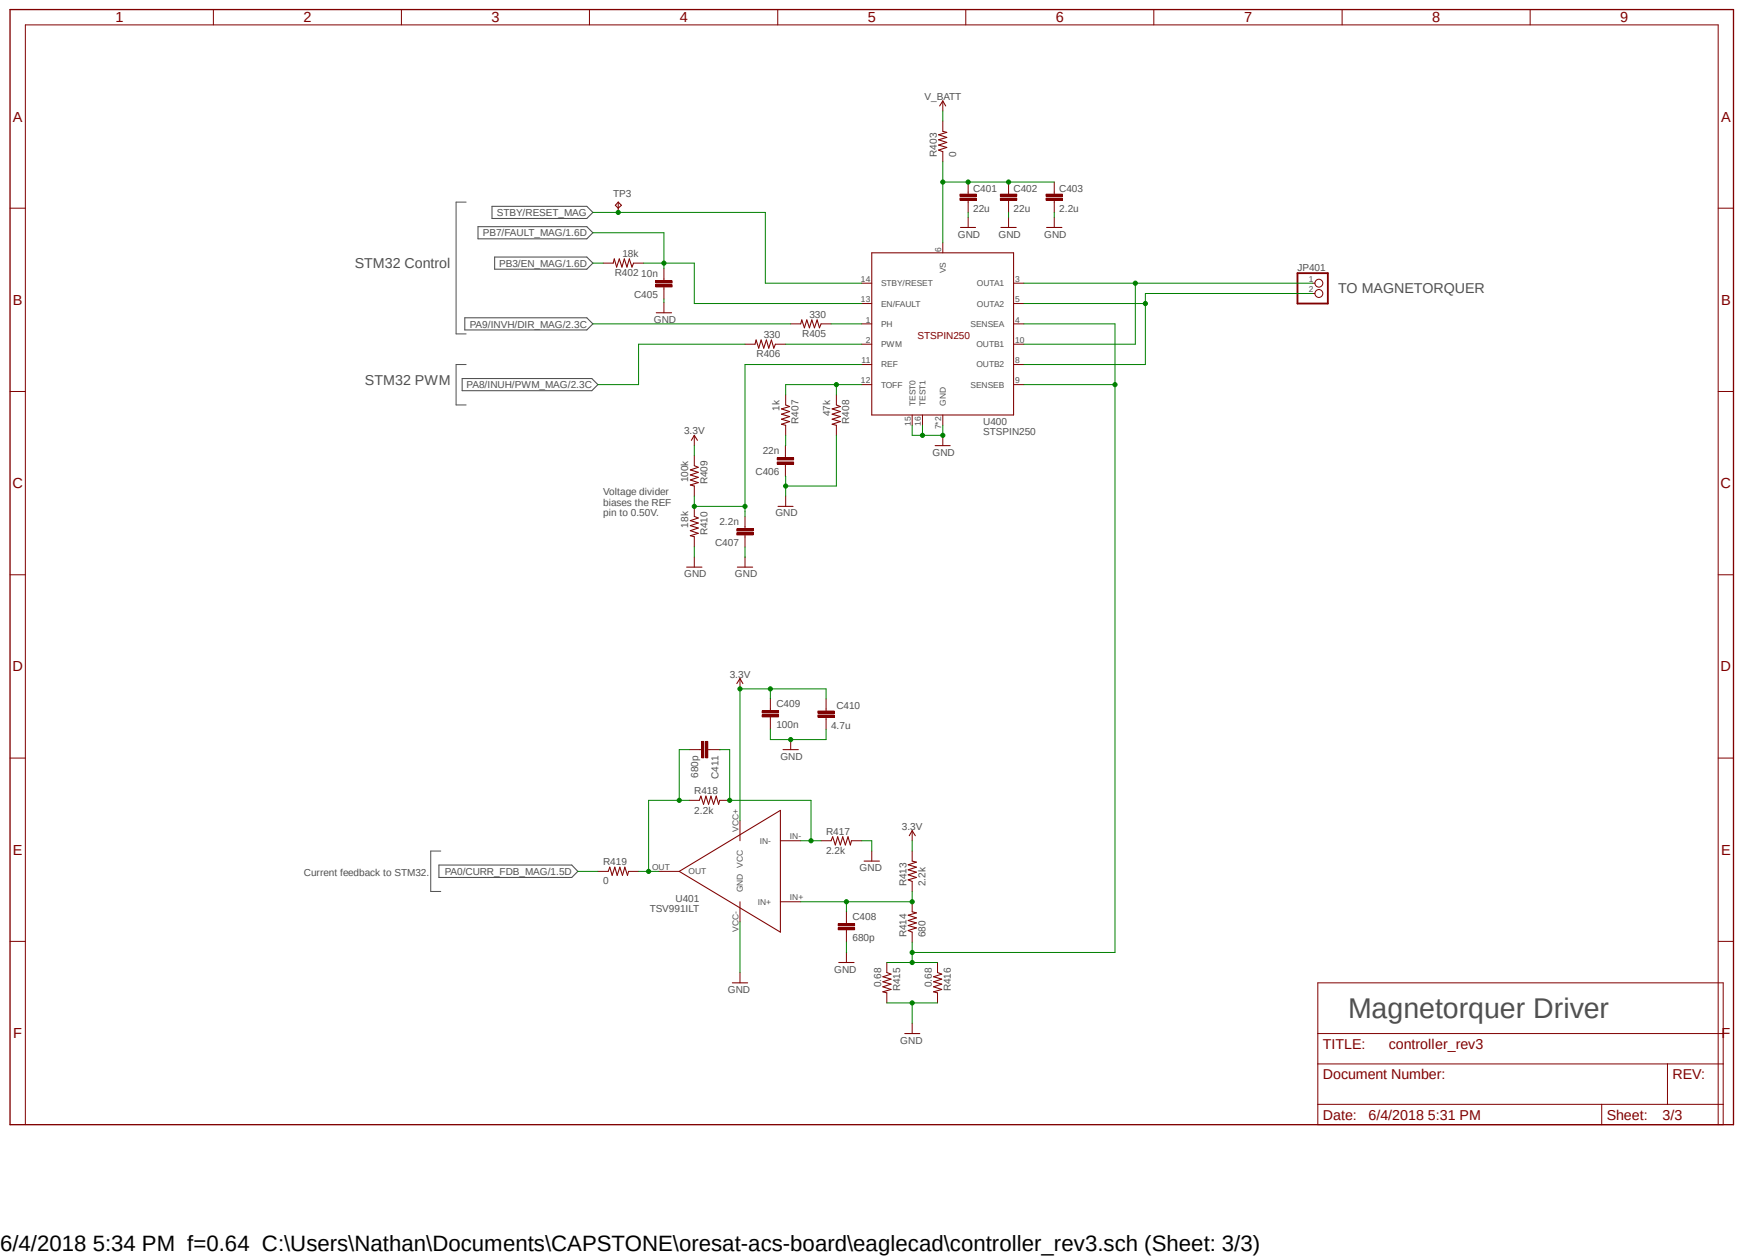
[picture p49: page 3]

0 STBY/RESET 14 EN/FAULT 13 PH 1 PWM 2 REF 11 TOFF 12 OUTA1 3 OUTA2 5 SENSEA 4 OUTB1 10 OUTB2 8 SENSEB 9 TEST0 15 TEST1 16 GND 7*2 VS

Voltage divider biases the REF

Magnetorquer Driver Current feedback to STM32.

Document Number: | REV:

Date: 6/4/2018 5:31 PM | Sheet: 3/3

6/4/2018 5:34 PM f=0.64 C:\Users\Nathan\Documents\CAPSTONE\oresat-acs-board\eaglecad\controller_rev3.sch (Sheet: 3/3)

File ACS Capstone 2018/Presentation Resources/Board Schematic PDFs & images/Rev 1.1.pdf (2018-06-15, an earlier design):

A

B

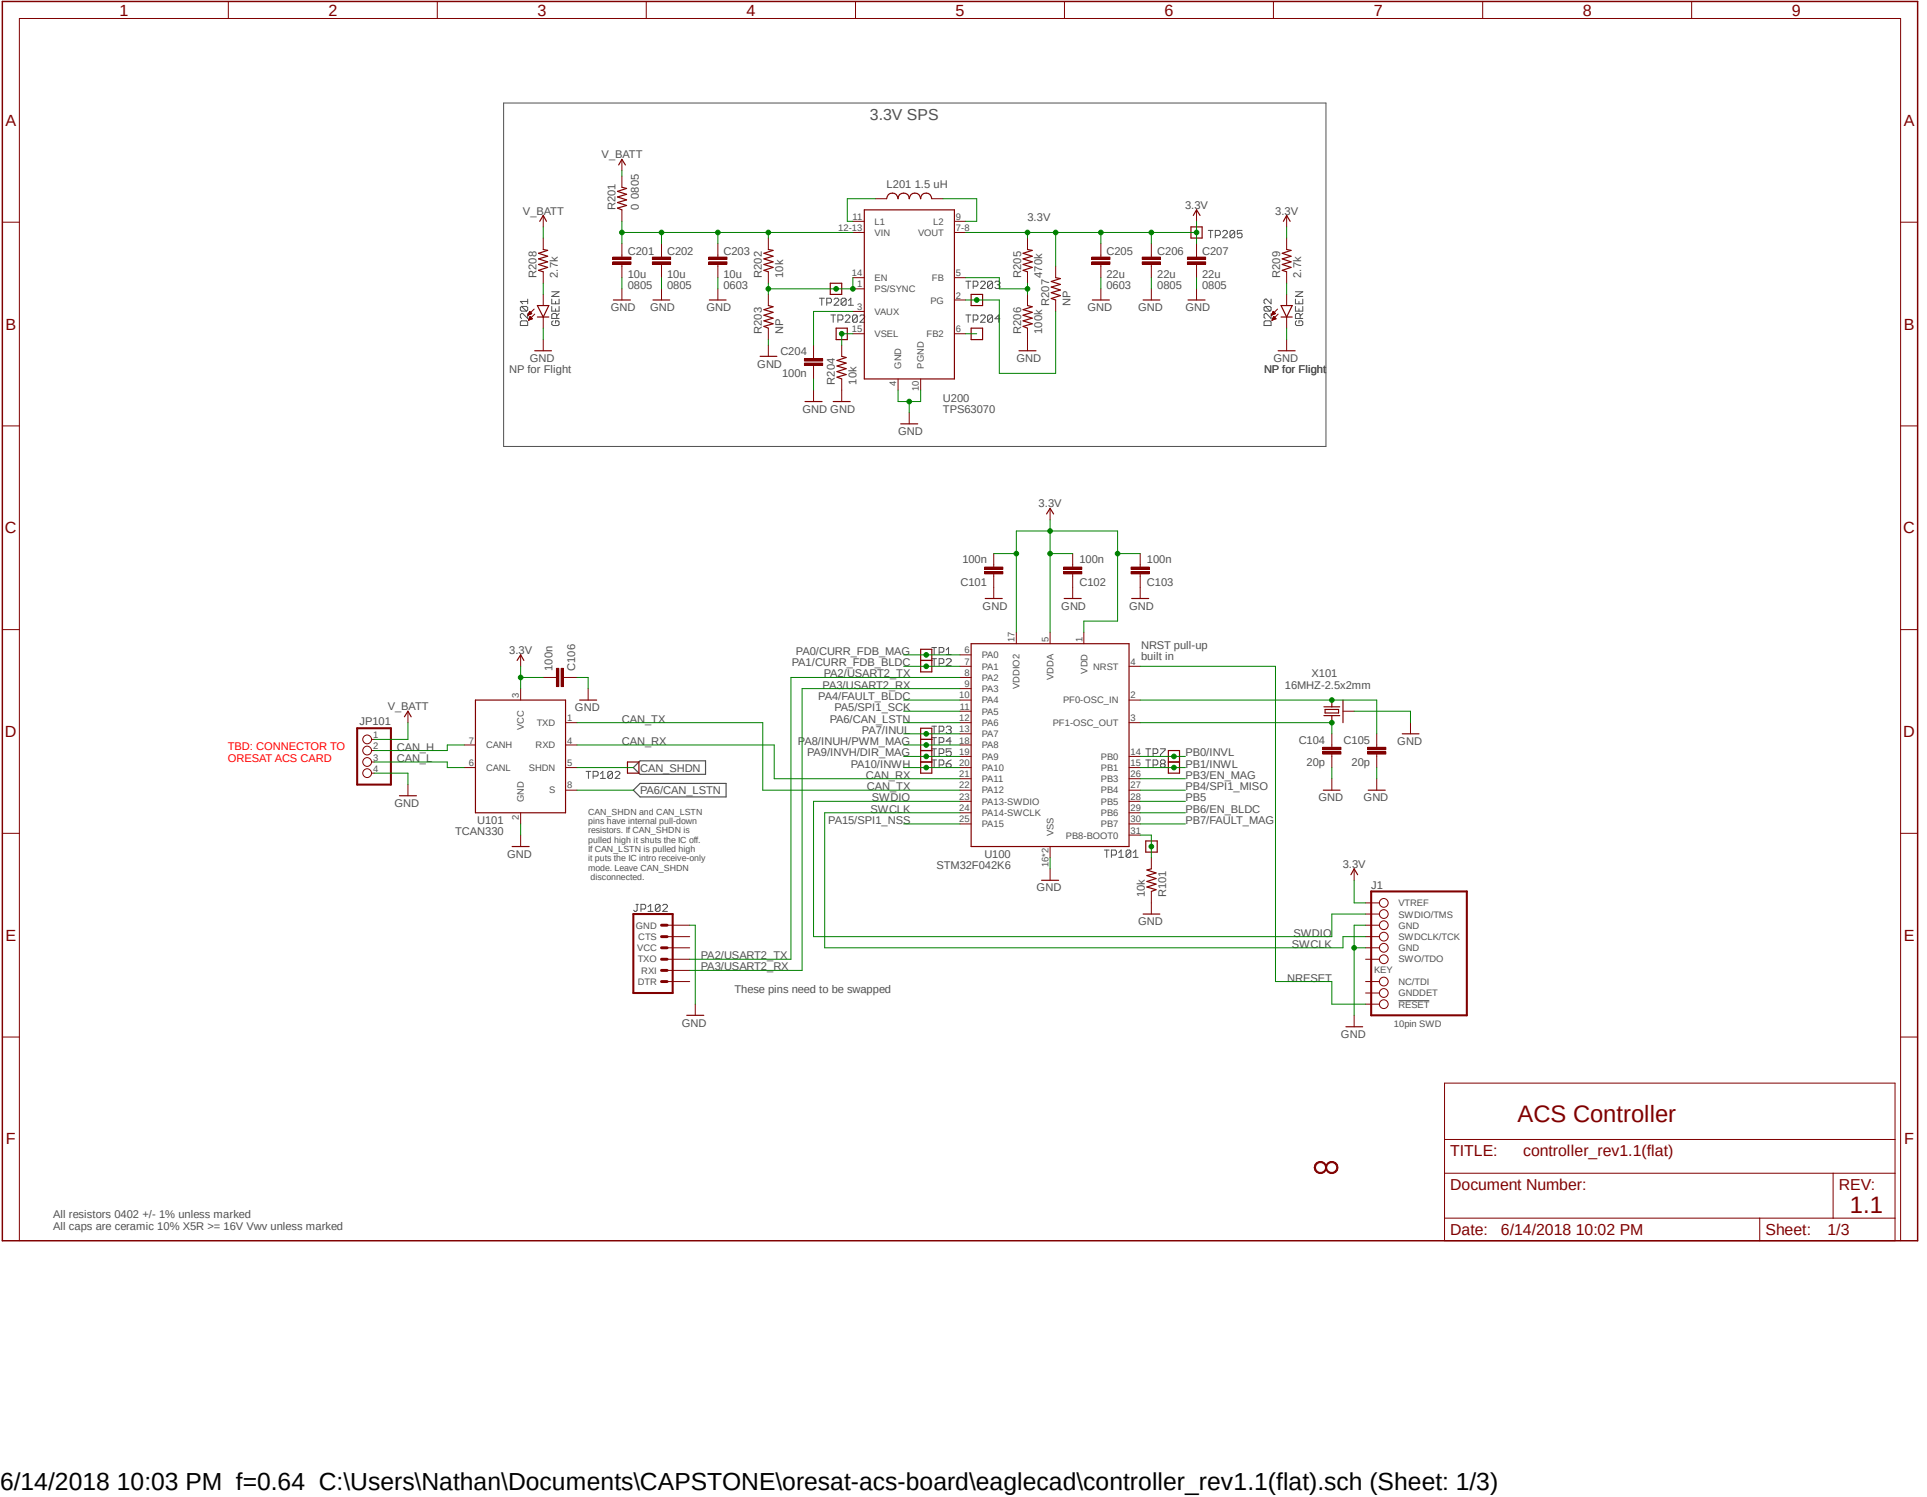
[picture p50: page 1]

NC/TDI GNDDET RESET CAN_TX CAN_TX
SWCLK CAN_RX CAN_RX

TBD: CONNECTOR TO ORESAT ACS CARD

CAN_SHDN and CAN_LSTN
pins have internal pull-down
resistors. If CAN_SHDN is pulled high it shuts the IC off.

If CAN_LSTN is pulled high
it puts the IC intro receive-only mode. Leave CAN_SHDN

Document Number: | REV: 1.1

All resistors 0402 +/- 1% unless marked All caps are ceramic 10% X5R >= 16V Vwv unless marked

Date: 6/14/2018 10:02 PM | Sheet: 1/3

6/14/2018 10:03 PM f=0.64 C:\Users\Nathan\Documents\CAPSTONE\oresat-acs-board\eaglecad\controller_rev1.1(flat).sch (Sheet: 1/3)

B

B

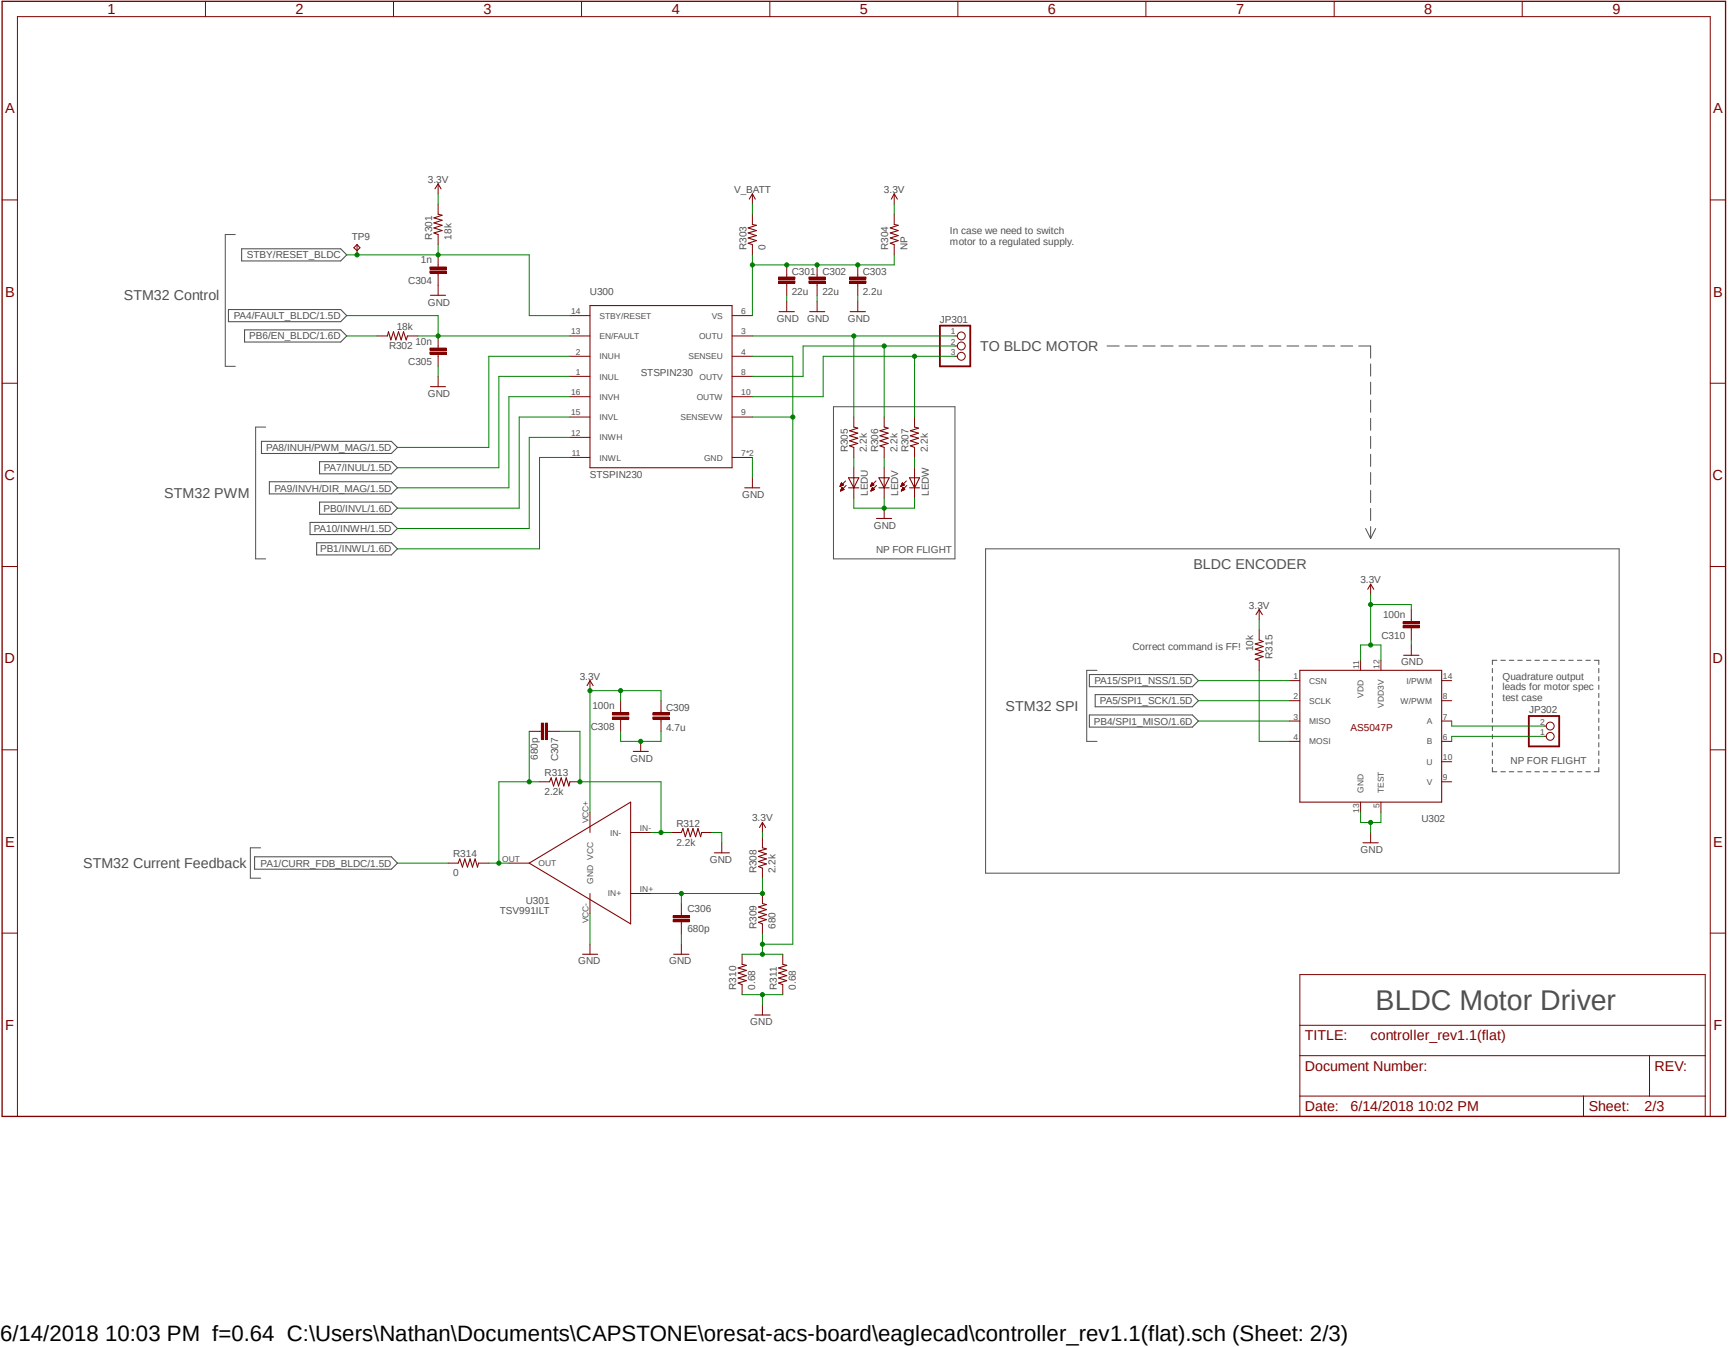
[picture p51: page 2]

INUL 1

INVL 15

NP FOR FLIGHT STM32 PWM

Correct command is FF! STM32 SPI

leads for motor spec
test case NP FOR FLIGHT

Document Number: | REV:

Date: 6/14/2018 10:02 PM | Sheet: 2/3

6/14/2018 10:03 PM f=0.64 C:\Users\Nathan\Documents\CAPSTONE\oresat-acs-board\eaglecad\controller_rev1.1(flat).sch (Sheet: 2/3)

## TO MAGNETORQUER

## STM32 Control

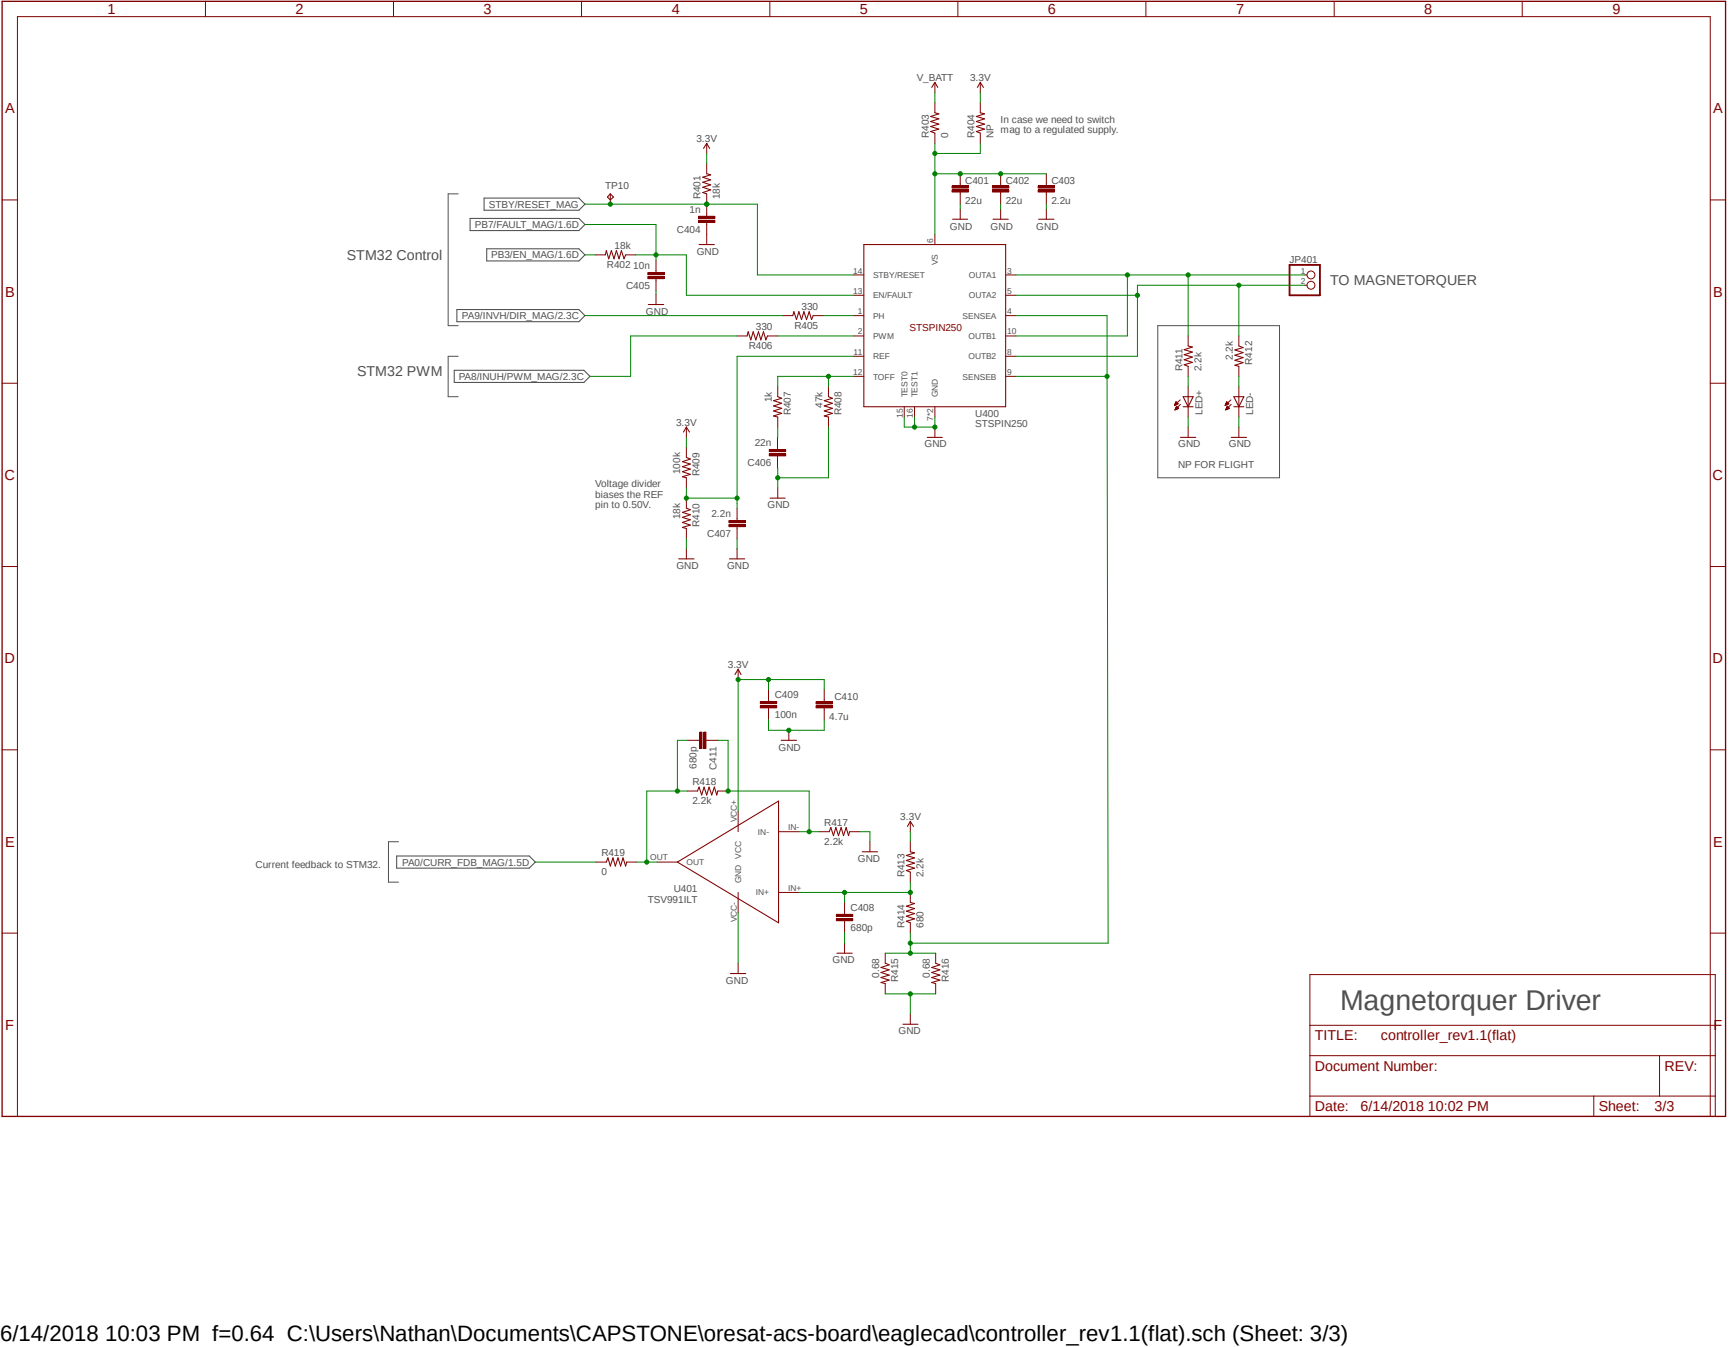
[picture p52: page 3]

In case we need to switch mag to a regulated supply. STSPIN250 GND

Voltage divider biases the REF

Magnetorquer Driver Current feedback to STM32.

Document Number: | REV:

Date: 6/14/2018 10:02 PM | Sheet: 3/3

6/14/2018 10:03 PM f=0.64 C:\Users\Nathan\Documents\CAPSTONE\oresat-acs-board\eaglecad\controller_rev1.1(flat).sch (Sheet: 3/3)

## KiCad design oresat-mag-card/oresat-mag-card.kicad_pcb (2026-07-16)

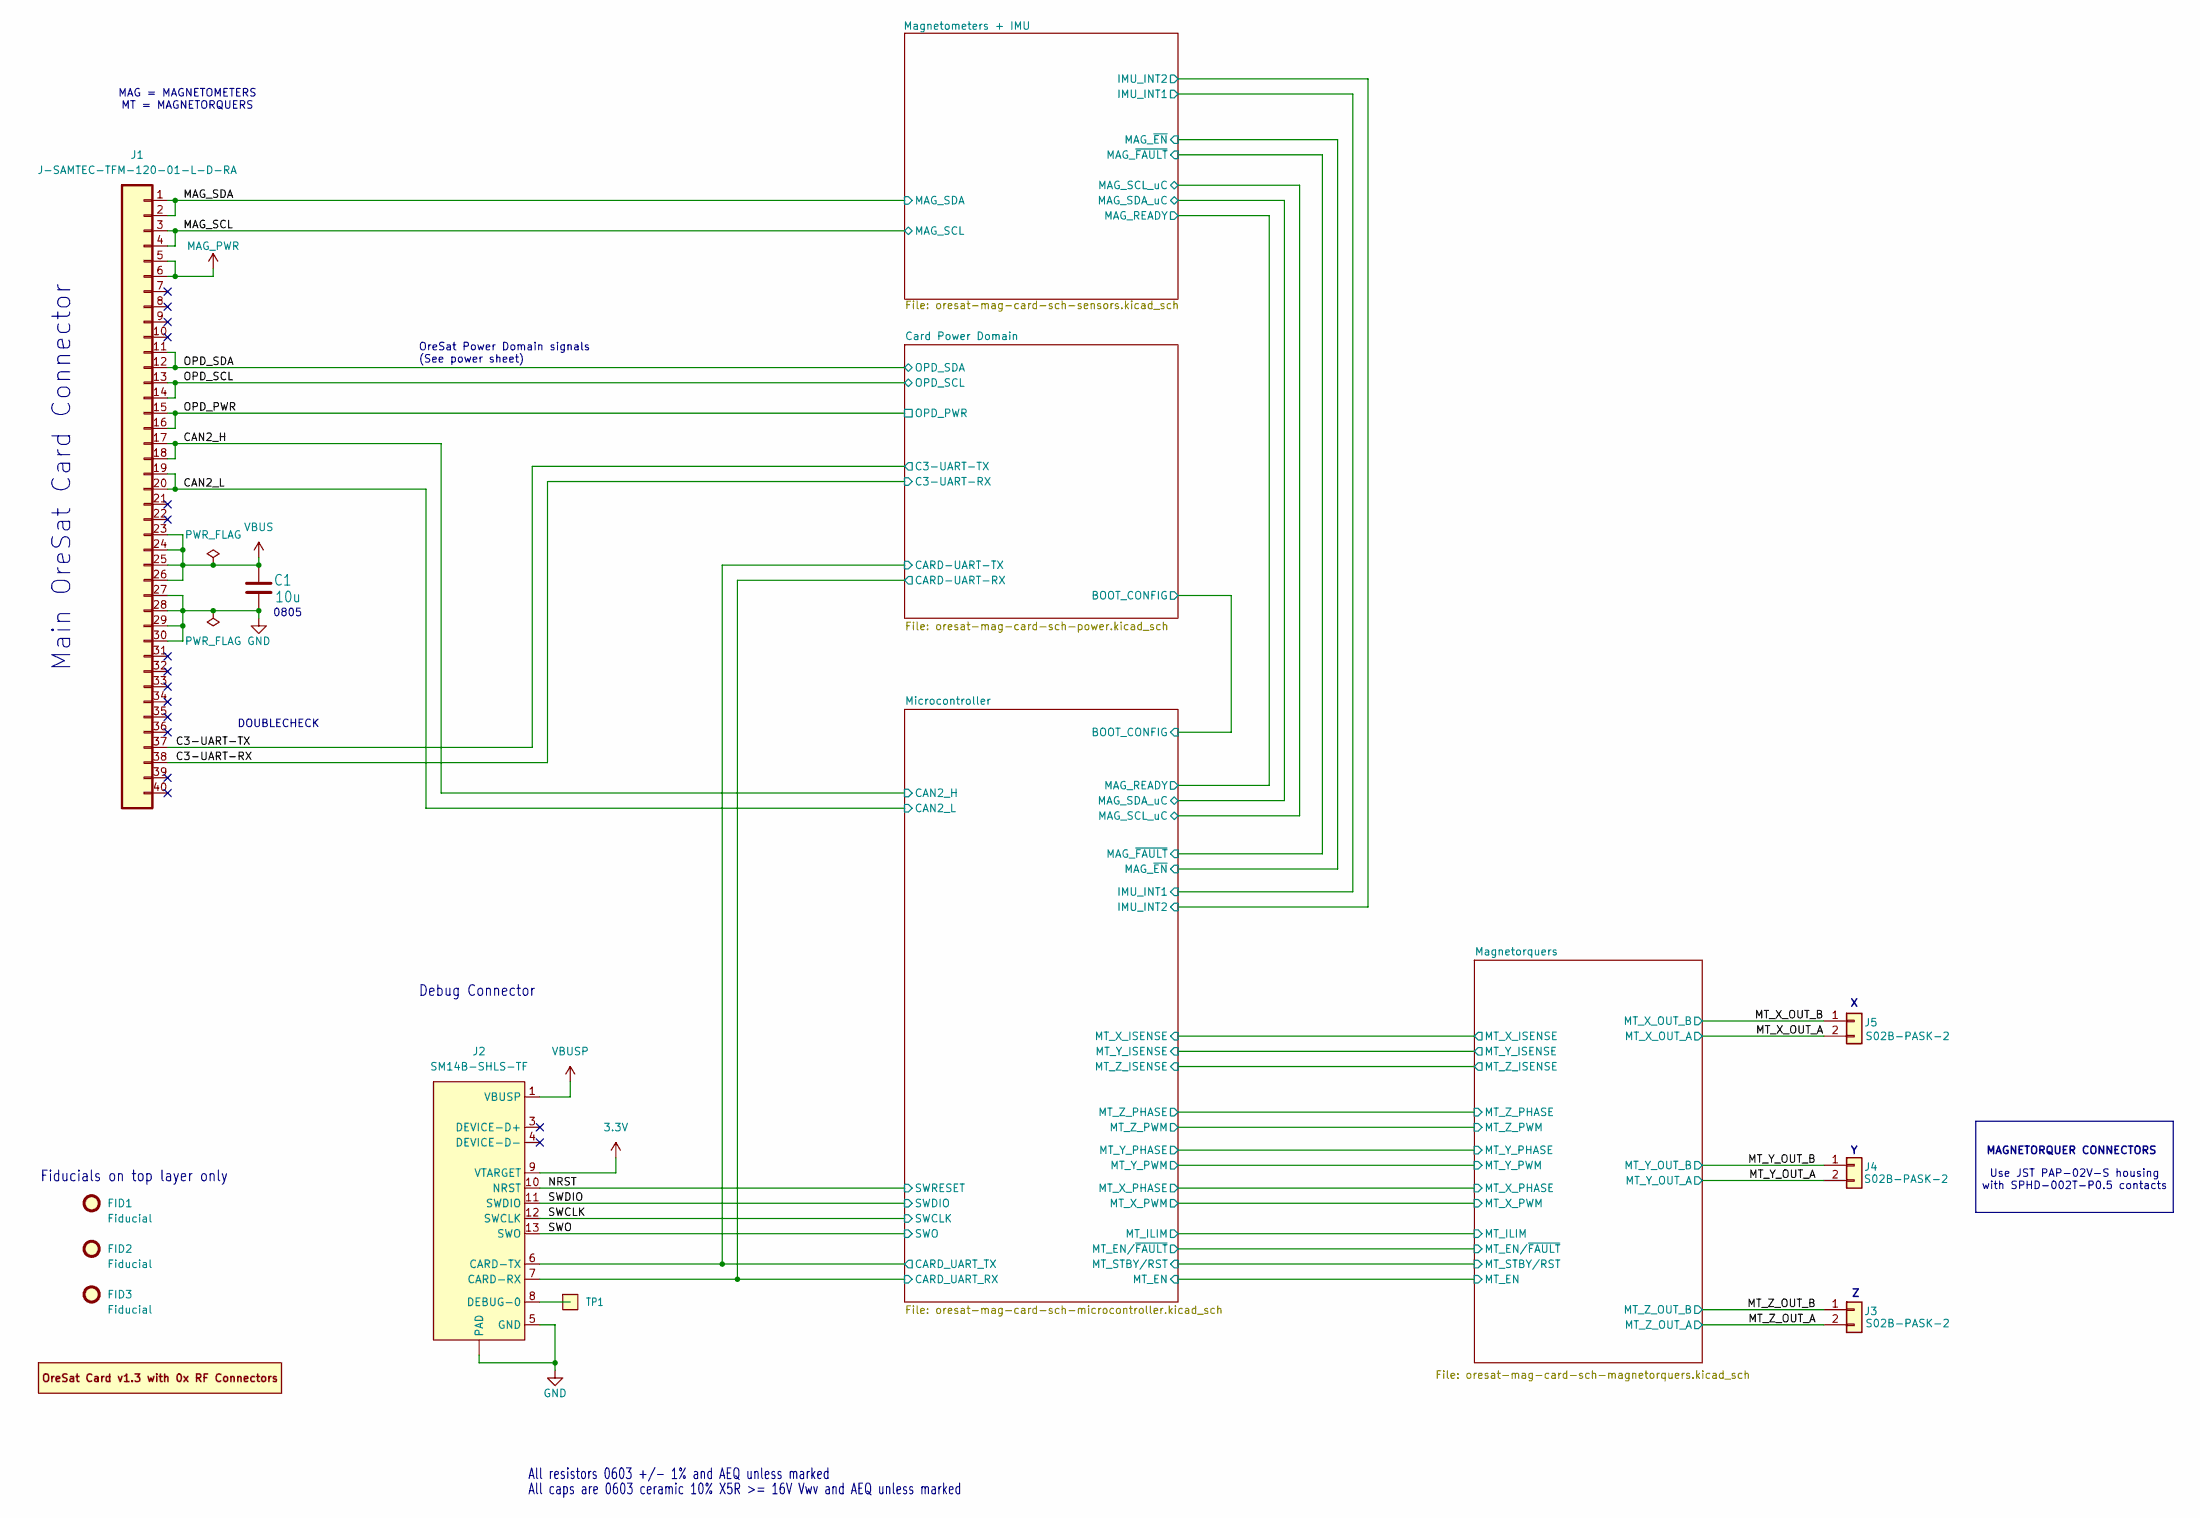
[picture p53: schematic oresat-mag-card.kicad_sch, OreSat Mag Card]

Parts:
C1: 10u; 0805-B-NOSILK; MPN GRT21BC71E106KE13K
FID1, FID2, FID3: Fiducial; Fiducial_1mm_Mask2mm
J1: J-SAMTEC-TFM-120-01-L-D-RA; J-SAMTEC-TFM-120-X1-XXX-D-RA; MPN TFM-120-01-L-D-RA
J2: SM14B-SHLS-TF; J-JST-SM14BSHLSTF; MPN SM14B-SHLS-TF
J3, J4, J5: S02B-PASK-2; JST-S02BPASK2LFSN; MPN S02B-PASK-2
PCB1: ORESAT-CARD-V1.3-GENERIC-0RF; ORESAT-CARD-V1.3-0RF; MPN N/A
TP1: Test-Point; TestPoint-0.75mm-th

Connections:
3.3V: J2.9 (VTARGET); also elsewhere on the board
/C3-UART-RX: J1.38; also elsewhere on the board
/C3-UART-TX: J1.37; also elsewhere on the board
/CAN2_H: J1.17, J1.18; also elsewhere on the board
/CAN2_L: J1.19, J1.20; also elsewhere on the board
/Card Power Domain/CARD-UART-RX: J2.7 (CARD-RX); also elsewhere on the board
/Card Power Domain/CARD-UART-TX: J2.6 (CARD-TX); also elsewhere on the board
/MAG_SCL: J1.3, J1.4; also elsewhere on the board
/MAG_SDA: J1.1, J1.2; also elsewhere on the board
/MT_X_OUT_A: J5.2; also elsewhere on the board
/MT_X_OUT_B: J5.1; also elsewhere on the board
/MT_Y_OUT_A: J4.2; also elsewhere on the board
/MT_Y_OUT_B: J4.1; also elsewhere on the board
/MT_Z_OUT_A: J3.2; also elsewhere on the board
/MT_Z_OUT_B: J3.1; also elsewhere on the board
/NRST: J2.10 (NRST); also elsewhere on the board
/OPD_PWR: J1.15, J1.16; also elsewhere on the board
/OPD_SCL: J1.13, J1.14; also elsewhere on the board
/OPD_SDA: J1.11, J1.12; also elsewhere on the board
/SWCLK: J2.12 (SWCLK); also elsewhere on the board
/SWDIO: J2.11 (SWDIO); also elsewhere on the board
/SWO: J2.13 (SWO); also elsewhere on the board
GND: C1.2, J1.27, J1.28, J1.29, J1.30, J2.5 (GND), J2.14 (GND), J2.15 (PAD), J2.16 (PAD); also elsewhere on the board
MAG_PWR: J1.5, J1.6; also elsewhere on the board
unnamed: J2.8 (DEBUG-0), TP1.1 (1_1)
VBUS: C1.1, J1.23, J1.24, J1.25, J1.26; also elsewhere on the board
VBUSP: J2.1 (VBUSP), J2.2 (VBUSP); also elsewhere on the board

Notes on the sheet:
All caps are 0603 ceramic 10% X5R >= 16V Vwv and AEQ unless marked
Main OreSat Card Connector
MAG = MAGNETOMETERS MT = MAGNETORQUERS
Use JST PAP-02V-S housing with SPHD-002T-P0.5 contacts
MAGNETORQUER CONNECTORS
DOUBLECHECK
Debug Connector
Fiducials on top layer only
0805
OreSat Power Domain signals (See power sheet)
All resistors 0603 +/- 1% and AEQ unless marked

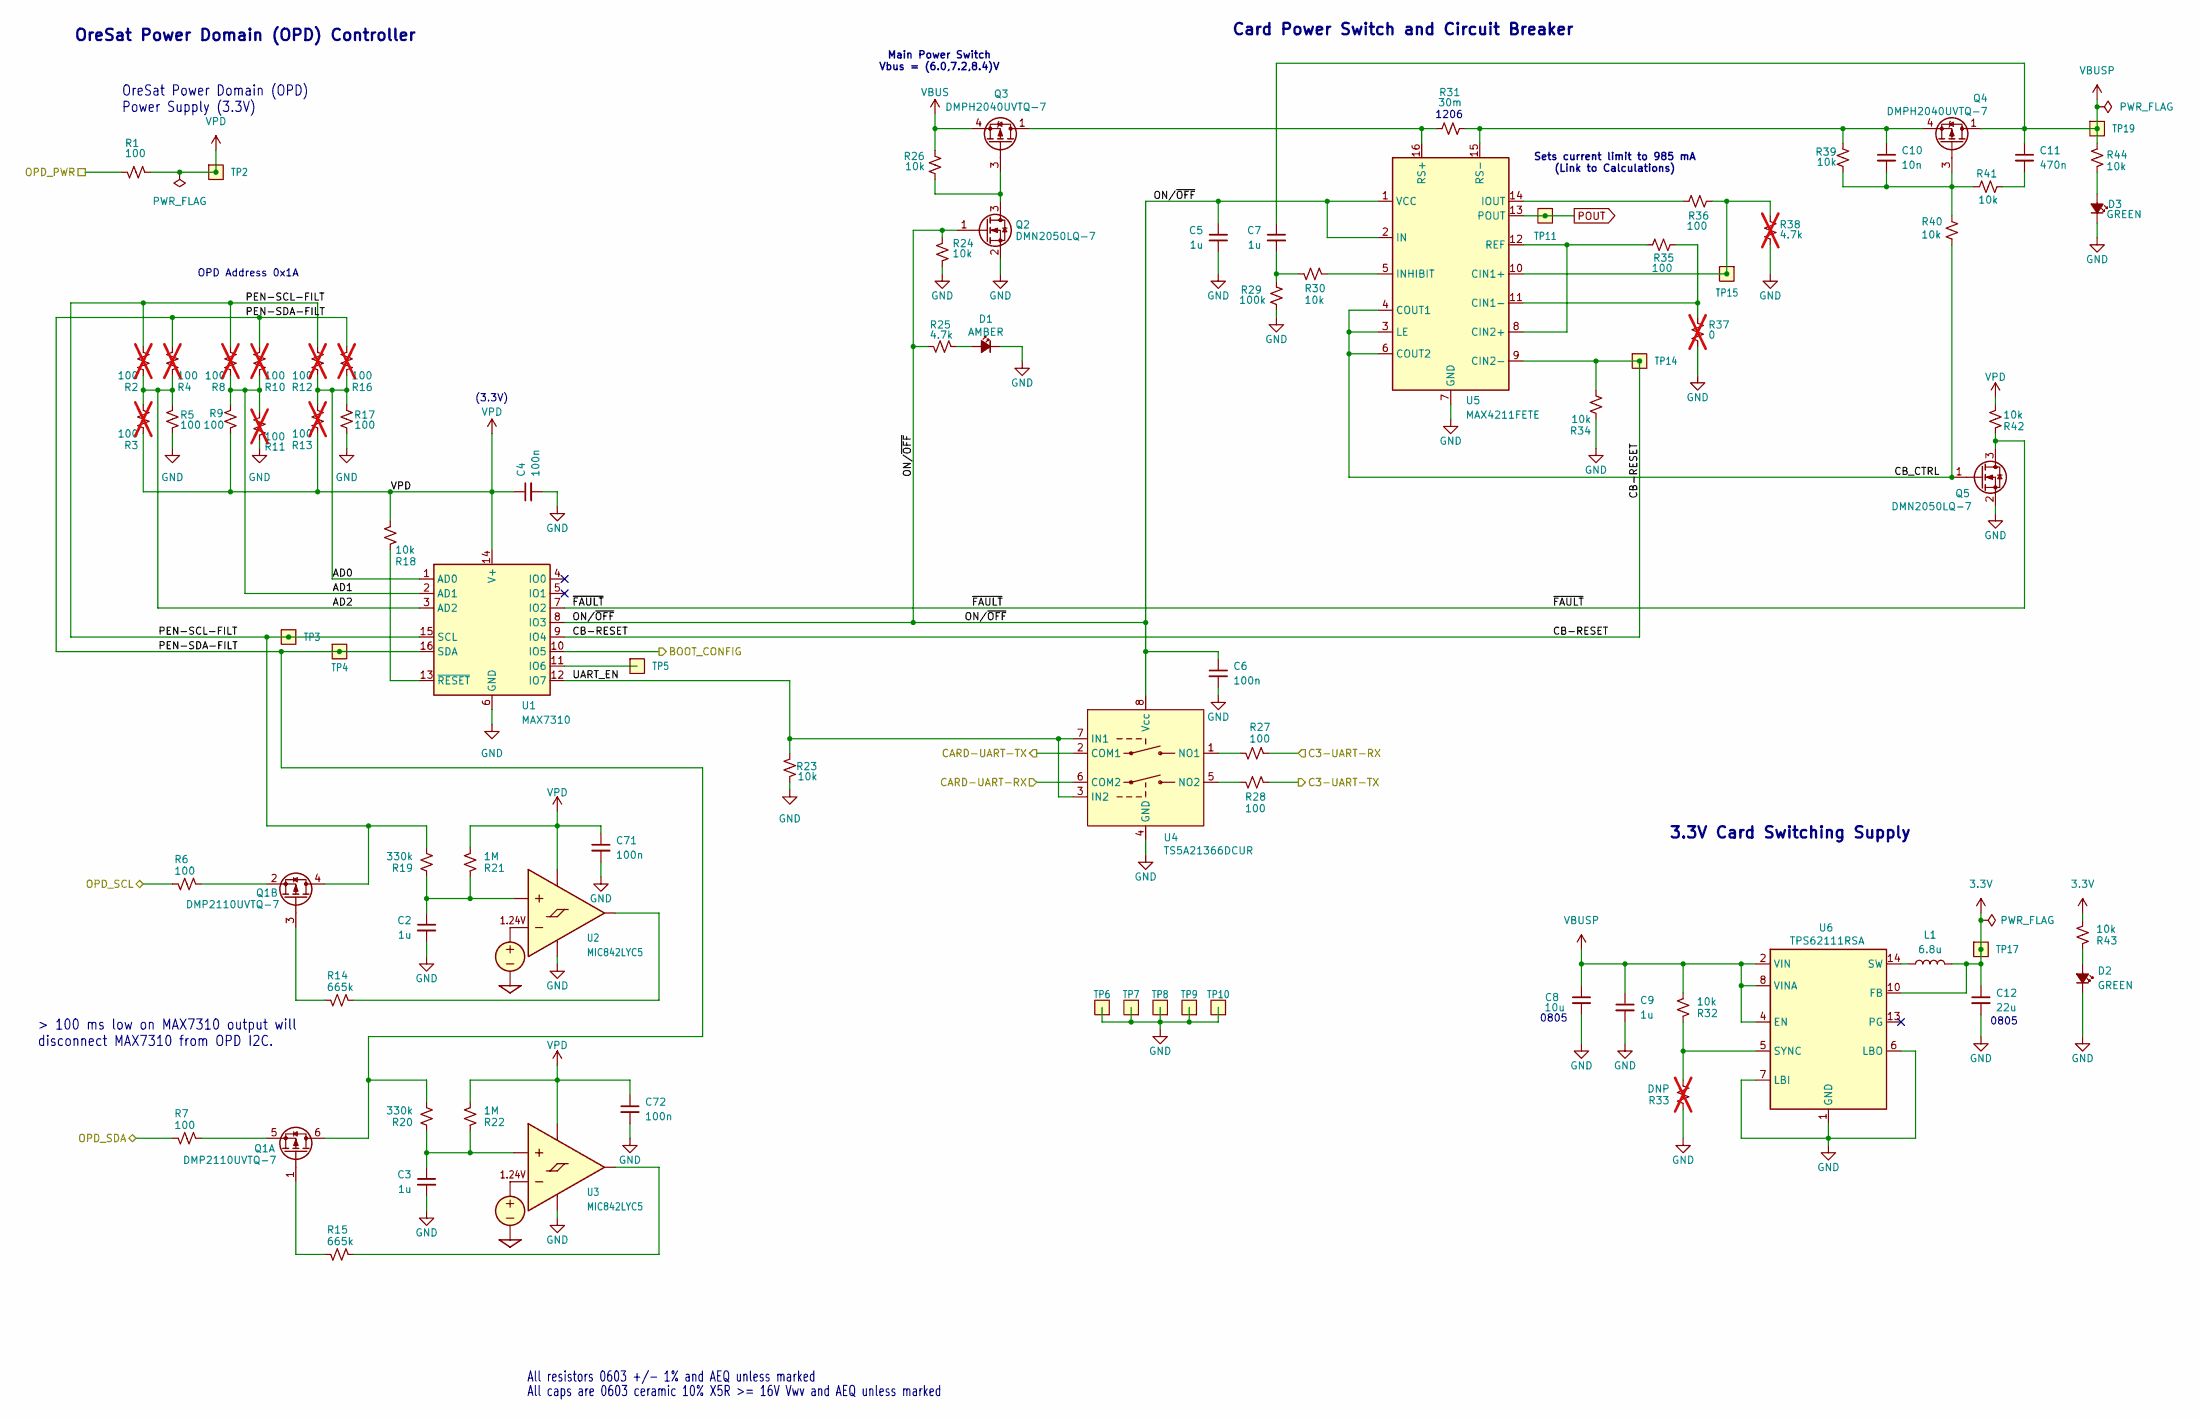
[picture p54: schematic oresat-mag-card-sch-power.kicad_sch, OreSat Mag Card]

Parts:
C2, C3, C5, C7, C9: 1u; 0603-C-NOSILK; MPN GRT188R71E105KE13D
C4, C6, C71, C72: 100n; 0603-C-NOSILK; MPN C0603C104K5RACAUTO
C8: 10u; 0805-B-NOSILK; MPN GRT21BC71E106KE13K
C10: 10n; 0603-C-NOSILK; MPN C0603C103J5RACAUTO
C11: 470n; 0603-C-NOSILK; MPN C0603C474K3RACAUTO
C12: 22u; 0805-B-NOSILK; MPN GRT21BC81C226ME13L
D1: AMBER; LED_0603_1608Metric; MPN 150060AS75000
D2, D3: GREEN; LED_0603_1608Metric; MPN 150060GS75000
L1: 6.8u; L_ECS-MPI4040; MPN ECS-MPI4040R4-6R8-R
Q1: DMP2110UVTQ-7; SOT-23-6; MPN DMP2110UVTQ-7
Q2, Q5: DMN2050LQ-7; SOT-23; MPN DMN2050LQ-7
Q3, Q4: DMPH2040UVTQ-7; TSOT-23-6; MPN DMPH2040UVTQ-7
R1, R5, R6, R7, R9, R17, R27, R28, R35, R36: 100; 0603-C-NOSILK; MPN RMCF0603FT100R
R2, R3, R4, R8, R10, R11, R12, R13, R16: 100; 0603-C-NOSILK; MPN RMCF0603FT100R; not fitted
R14, R15: 665k; 0603-C-NOSILK; MPN RMCF0603FT665K
R18, R23, R24, R26, R30, R32, R34, R39, R40, R41, R42, R43, R44: 10k; 0603-C-NOSILK; MPN RMCF0603FT10K0
R19, R20: 330k; 0603-C-NOSILK; MPN RMCF0603FT330K
R21, R22: 1M; 0603-C-NOSILK; MPN RMCF0603FT1M00
R25: 4.7k; 0603-C-NOSILK; MPN RMCF0603FT4K70
R29: 100k; 0603-C-NOSILK; MPN RMCF0603FT100K
R31: 30m; 1206-C; MPN CSR1206FK30L0
R33: DNP; 0603-C-NOSILK; not fitted
R37: 0; 0603-C-NOSILK; MPN RMCF0603ZT0R00; not fitted
R38: 4.7k; 0603-C-NOSILK; MPN RMCF0603FT4K70; not fitted
TP2, TP3, TP4, TP5, TP6, TP7, TP8, TP9, TP10, TP11, TP14, TP15, TP17, TP19: Test-Point; TestPoint-0.75mm-th
U1: MAX7310; QFN-16-1EP_4x4mm_P0.65mm_EP2.1x2.1mm; MPN MAX7310ATE+
U2, U3: MIC842LYC5; SOT-353_SC-70-5; MPN MIC842LYC5-TR
U4: TS5A21366DCUR; VSSOP-8_2.3x2mm_P0.5mm; MPN TS5A21366DCUR
U5: MAX4211FETE; QFN-16-1EP_4x4mm_P0.65mm_EP2.1x2.1mm; MPN MAX4211FETE
U6: TPS62111RSA; Texas_RSA_VQFN-16-1EP_4x4mm_P0.65mm_EP2.7x2.7mm; MPN TPS62111RSA

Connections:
3.3V: C12.1, L1.2, R43.2, TP17.1 (1_1), U6.10 (FB); also elsewhere on the board
/C3-UART-RX: R27.1; also elsewhere on the board
/C3-UART-TX: R28.1; also elsewhere on the board
/Card Power Domain/AD0: R12.1, R13.2, R16.1, R17.2, U1.1 (AD0)
/Card Power Domain/AD1: R8.1, R9.2, R10.1, R11.2, U1.2 (AD1)
/Card Power Domain/AD2: R2.1, R3.2, R4.1, R5.2, U1.3 (AD2)
/Card Power Domain/BOOT_CONFIG: U1.10 (IO5); also elsewhere on the board
/Card Power Domain/CARD-UART-RX: U4.6 (COM2); also elsewhere on the board
/Card Power Domain/CARD-UART-TX: U4.2 (COM1); also elsewhere on the board
/Card Power Domain/CB-RESET: R34.2, TP14.1 (1_1), U1.9 (IO4), U5.9 (CIN2-)
/Card Power Domain/CB_CTRL: Q5.1 (G), R40.1, U5.3 (LE), U5.4 (COUT1), U5.6 (COUT2)
/Card Power Domain/ON/~OFF: C5.1, C6.1, Q2.1 (G), R24.1, R25.2, U1.8 (IO3), U4.8 (Vcc), U5.1 (VCC), U5.2 (IN)
/Card Power Domain/PEN-SCL-FILT: Q1.4 (D), R2.2, R8.2, R12.2, R19.2, TP3.1 (1_1), U1.15 (SCL)
/Card Power Domain/PEN-SDA-FILT: Q1.6 (D), R4.2, R10.2, R16.2, R20.2, TP4.1 (1_1), U1.16 (SDA)
/Card Power Domain/UART_EN: R23.2, U1.12 (IO7), U4.3 (IN2), U4.7 (IN1)
/Card Power Domain/~FAULT: Q5.3 (D), R42.1, U1.7 (IO2)
/OPD_PWR: R1.2; also elsewhere on the board
/OPD_SCL: R6.2; also elsewhere on the board
/OPD_SDA: R7.2; also elsewhere on the board
GND: C2.2, C3.2, C4.2, C5.2, C6.2, C8.2, C9.2, C12.2, C71.2, C72.2, D1.1 (K), D2.1 (K), D3.1 (K), Q2.2 (S), Q5.2 (S), R5.1, R11.1, R17.1, R23.1, R24.2, R29.2, R33.1, R34.1, R37.2, R38.2, TP6.1 (1_1), TP7.1 (1_1), TP8.1 (1_1), TP9.1 (1_1), TP10.1 (1_1), U1.6 (GND), U1.17 (GND), U2.2 (GND), U3.2 (GND), U4.4 (GND), U5.7 (GND), U5.17 (GND), U6.1 (GND), U6.6 (LBO), U6.7 (LBI), U6.9 (GND), U6.11 (GND), U6.12 (GND), U6.16 (GND), U6.17 (GND); also elsewhere on the board
unnamed: C7.2, R29.1, R30.2
unnamed: C11.2, R41.1
unnamed: D1.2 (A), R25.1
unnamed: D2.2 (A), R43.1
unnamed: D3.2 (A), R44.1
unnamed: L1.1, U6.14 (SW), U6.15 (SW)
unnamed: Q1.1 (G), R15.2
unnamed: Q1.5 (S), R7.1
unnamed: Q1.3 (G), R14.2
unnamed: Q1.2 (S), R6.1
unnamed: Q2.3 (D), Q3.3 (G), R26.2
unnamed: C10.2, Q4.3 (G), R39.1, R40.2, R41.2
unnamed: C10.1, Q4.4 (S), R31.2, R39.2, U5.15 (RS-)
unnamed: TP5.1 (1_1), U1.11 (IO6)
unnamed: R18.1, U1.13 (~RESET)
unnamed: C2.1, R19.1, R21.1, U2.1 (INP)
unnamed: R14.1, U2.4 (OUT)
unnamed: C3.1, R20.1, R22.1, U3.1 (INP)
unnamed: R15.1, U3.4 (OUT)
unnamed: R27.2, U4.1 (NO1)
unnamed: R28.2, U4.5 (NO2)
unnamed: R36.1, R38.1, TP15.1 (1_1), U5.10 (CIN1+)
unnamed: R35.1, R37.1, U5.11 (CIN1-)
unnamed: R35.2, U5.8 (CIN2+), U5.12 (REF)
unnamed: R30.1, U5.5 (INHIBIT)
unnamed: R36.2, U5.14 (IOUT)
unnamed: Q3.1 (D), Q3.2 (D), Q3.5 (D), Q3.6 (D), R31.1, U5.16 (RS+)
unnamed: R32.1, R33.2, U6.5 (SYNC)
POUT: TP11.1 (1_1), U5.13 (POUT)
VBUS: Q3.4 (S), R26.1; also elsewhere on the board
VBUSP: C7.1, C8.1, C9.1, C11.1, Q4.1 (D), Q4.2 (D), Q4.5 (D), Q4.6 (D), R32.2, R44.2, TP19.1 (1_1), U6.2 (VIN), U6.3 (VIN), U6.4 (EN), U6.8 (VINA); also elsewhere on the board
VPD: C4.1, C71.1, C72.1, R1.1, R3.1, R9.1, R13.1, R18.2, R21.2, R22.2, R42.2, TP2.1 (1_1), U1.14 (V+), U2.5 (VDD), U3.5 (VDD)

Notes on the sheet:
Sets current limit to 985 mA (Link to Calculations)
OPD Address 0x1A
3.3V Card Switching Supply
OreSat Power Domain (OPD) Power Supply (3.3V)
> 100 ms low on MAX7310 output will disconnect MAX7310 from OPD I2C.
Card Power Switch and Circuit Breaker
1206
(3.3V)
All resistors 0603 +/- 1% and AEQ unless marked
All caps are 0603 ceramic 10% X5R >= 16V Vwv and AEQ unless marked
OreSat Power Domain (OPD) Controller
0805
Main Power Switch Vbus = (6.0,7.2,8.4)V

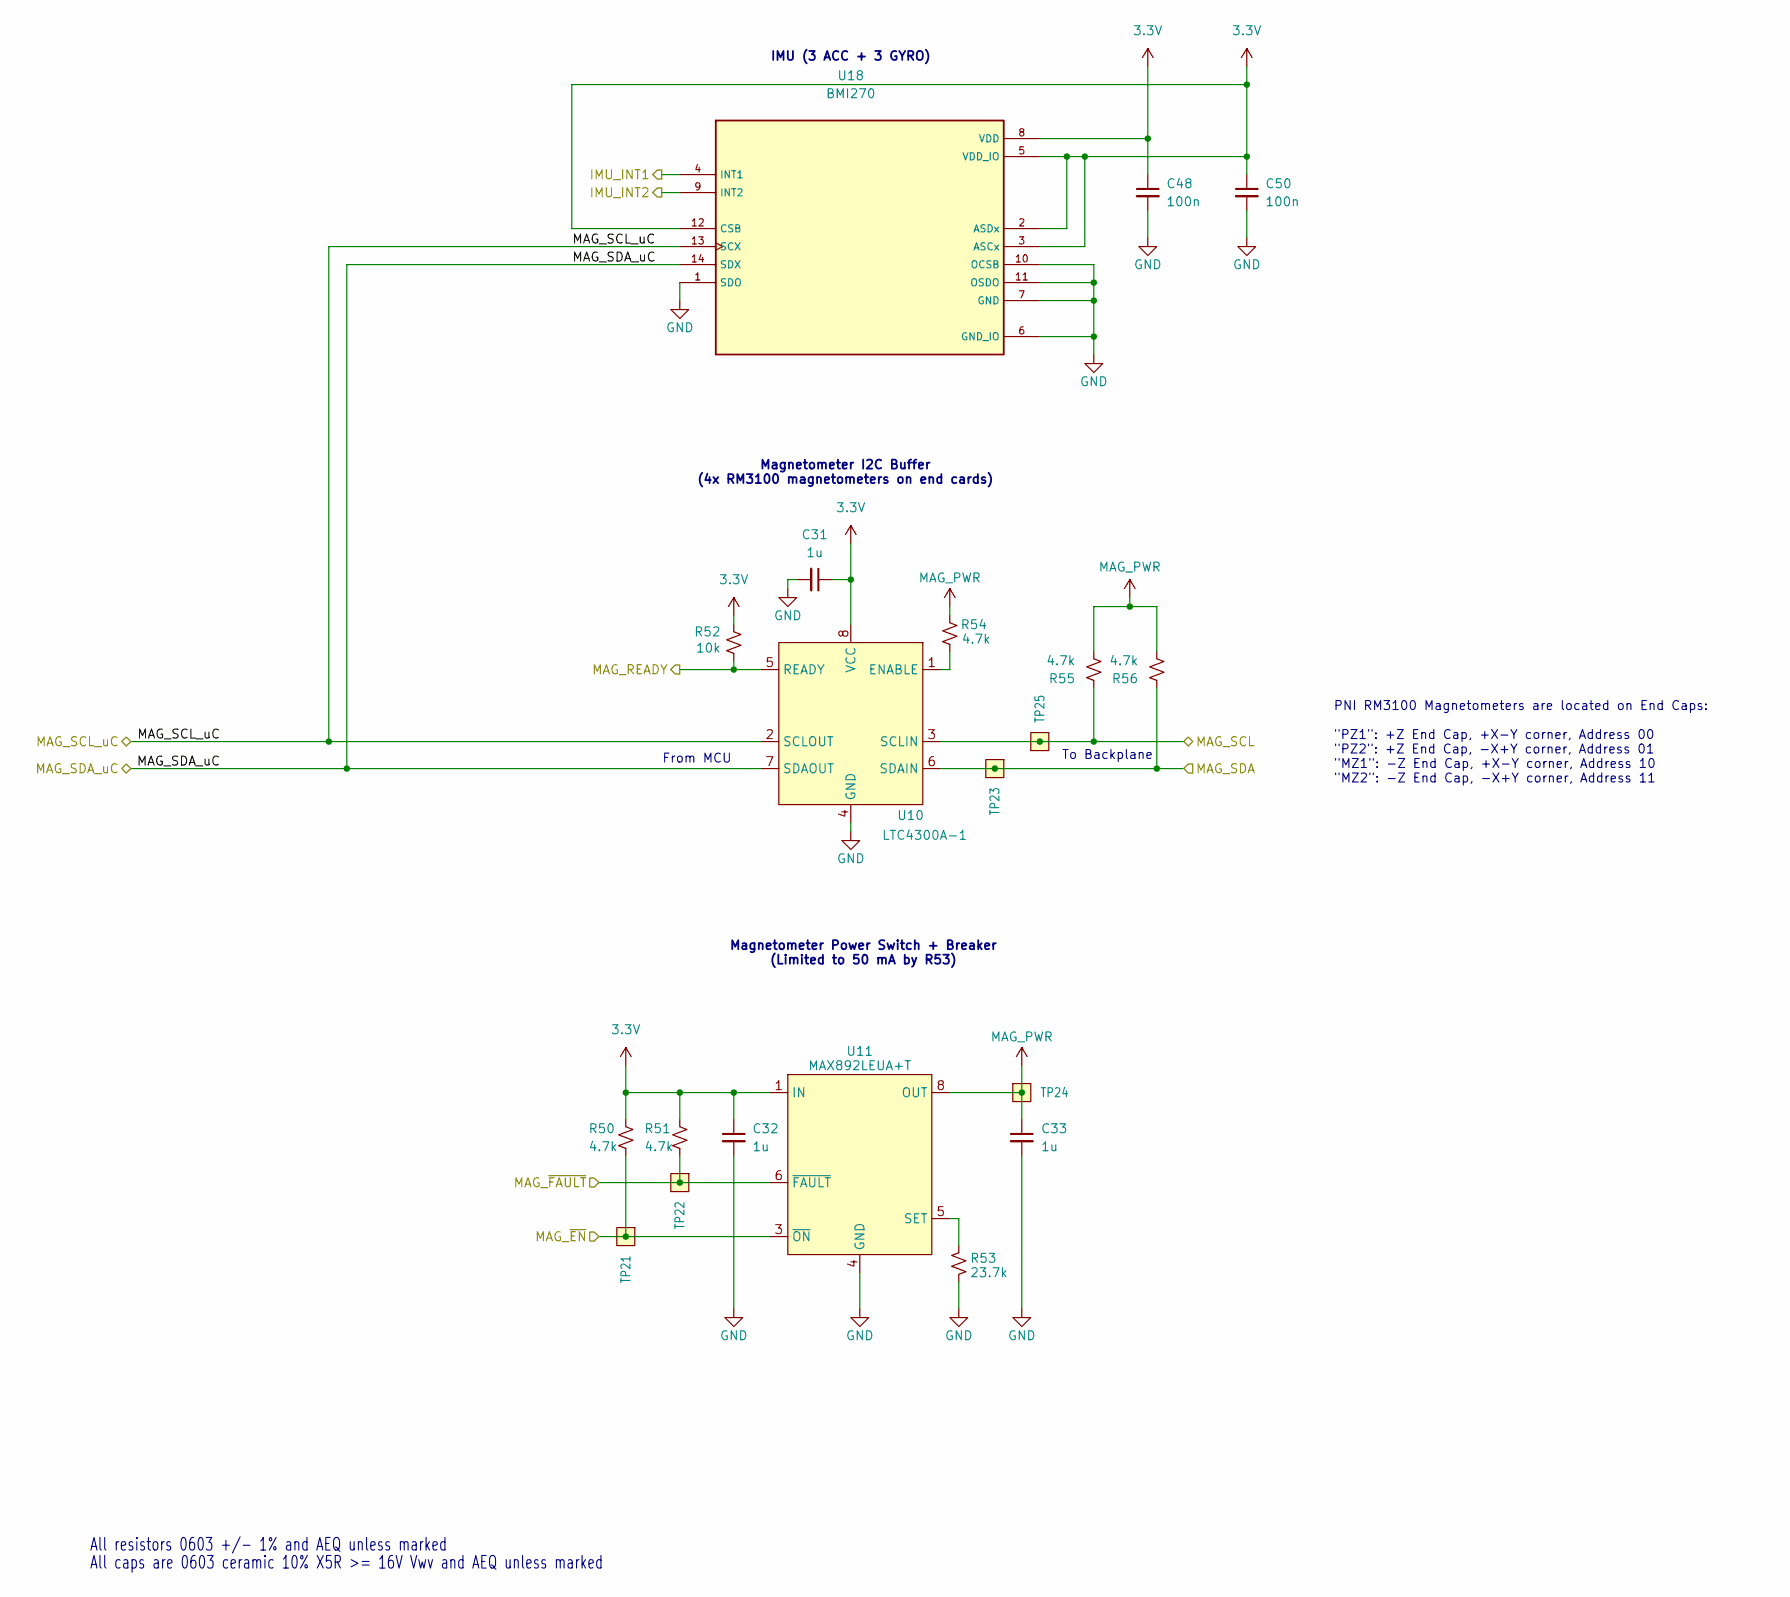
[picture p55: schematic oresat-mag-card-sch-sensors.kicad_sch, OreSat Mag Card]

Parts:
C31, C32, C33: 1u; 0603-C-NOSILK; MPN GRT188R71E105KE13D
C48, C50: 100n; 0603-C-NOSILK; MPN C0603C103J5RACAUTO
R50, R51, R54, R55, R56: 4.7k; 0603-C-NOSILK; MPN RMCF0603FT4K70
R52: 10k; 0603-C-NOSILK; MPN RMCF0603FT10K0
R53: 23.7k; 0603-C-NOSILK; MPN RMCF0603FT23K7
TP21, TP22, TP23, TP24, TP25: Test-Point; TestPoint-0.75mm-th
U10: LTC4300A-1; MSOP-8_3x3mm_P0.65mm; MPN LTC4300A-1IMS8#TRPBF
U11: MAX892LEUA+T; MSOP-8_3x3mm_P0.65mm; MPN MAX892LEUA+T
U18: BMI270; PQFN50P300X250X97-14N; MPN BMI270

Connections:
3.3V: C31.1, C32.1, C48.1, C50.1, R50.2, R51.2, R52.2, U10.8 (VCC), U11.1 (IN), U11.2 (IN_2), U18.2 (ASDx), U18.3 (ASCx), U18.5 (VDD_IO), U18.8 (VDD), U18.12 (CSB); also elsewhere on the board
/MAG_SCL: R55.1, TP25.1 (1_1), U10.3 (SCLIN); also elsewhere on the board
/MAG_SDA: R56.1, TP23.1 (1_1), U10.6 (SDAIN); also elsewhere on the board
/Magnetometers + IMU/IMU_INT1: U18.4 (INT1); also elsewhere on the board
/Magnetometers + IMU/IMU_INT2: U18.9 (INT2); also elsewhere on the board
/Magnetometers + IMU/MAG_READY: R52.1, U10.5 (READY); also elsewhere on the board
/Magnetometers + IMU/MAG_SCL_uC: U10.2 (SCLOUT), U18.13 (SCX); also elsewhere on the board
/Magnetometers + IMU/MAG_SDA_uC: U10.7 (SDAOUT), U18.14 (SDX); also elsewhere on the board
/Magnetometers + IMU/MAG_~EN: R50.1, TP21.1 (1_1), U11.3 (~ON); also elsewhere on the board
/Magnetometers + IMU/MAG_~FAULT: R51.1, TP22.1 (1_1), U11.6 (~FAULT); also elsewhere on the board
GND: C31.2, C32.2, C33.2, C48.2, C50.2, R53.1, U10.4 (GND), U11.4 (GND), U18.1 (SDO), U18.6 (GND_IO), U18.7 (GND), U18.10 (OCSB), U18.11 (OSDO); also elsewhere on the board
MAG_PWR: C33.1, R54.2, R55.2, R56.2, TP24.1 (1_1), U11.7 (OUT_2), U11.8 (OUT); also elsewhere on the board
unnamed: R54.1, U10.1 (ENABLE)
unnamed: R53.2, U11.5 (SET)

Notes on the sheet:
PNI RM3100 Magnetometers are located on End Caps: "PZ1": +Z End Cap, +X-Y corner, Address 00 "PZ2": +Z End Cap, -X+Y corner, Address 01 "MZ1": -Z End Cap, +X-Y corner, Address 10 "MZ2": -Z End Cap, -X+Y corner, Address 11
To Backplane
All resistors 0603 +/- 1% and AEQ unless marked
IMU (3 ACC + 3 GYRO)
From MCU
All caps are 0603 ceramic 10% X5R >= 16V Vwv and AEQ unless marked
Magnetometer Power Switch + Breaker (Limited to 50 mA by R53)
Magnetometer I2C Buffer (4x RM3100 magnetometers on end cards)

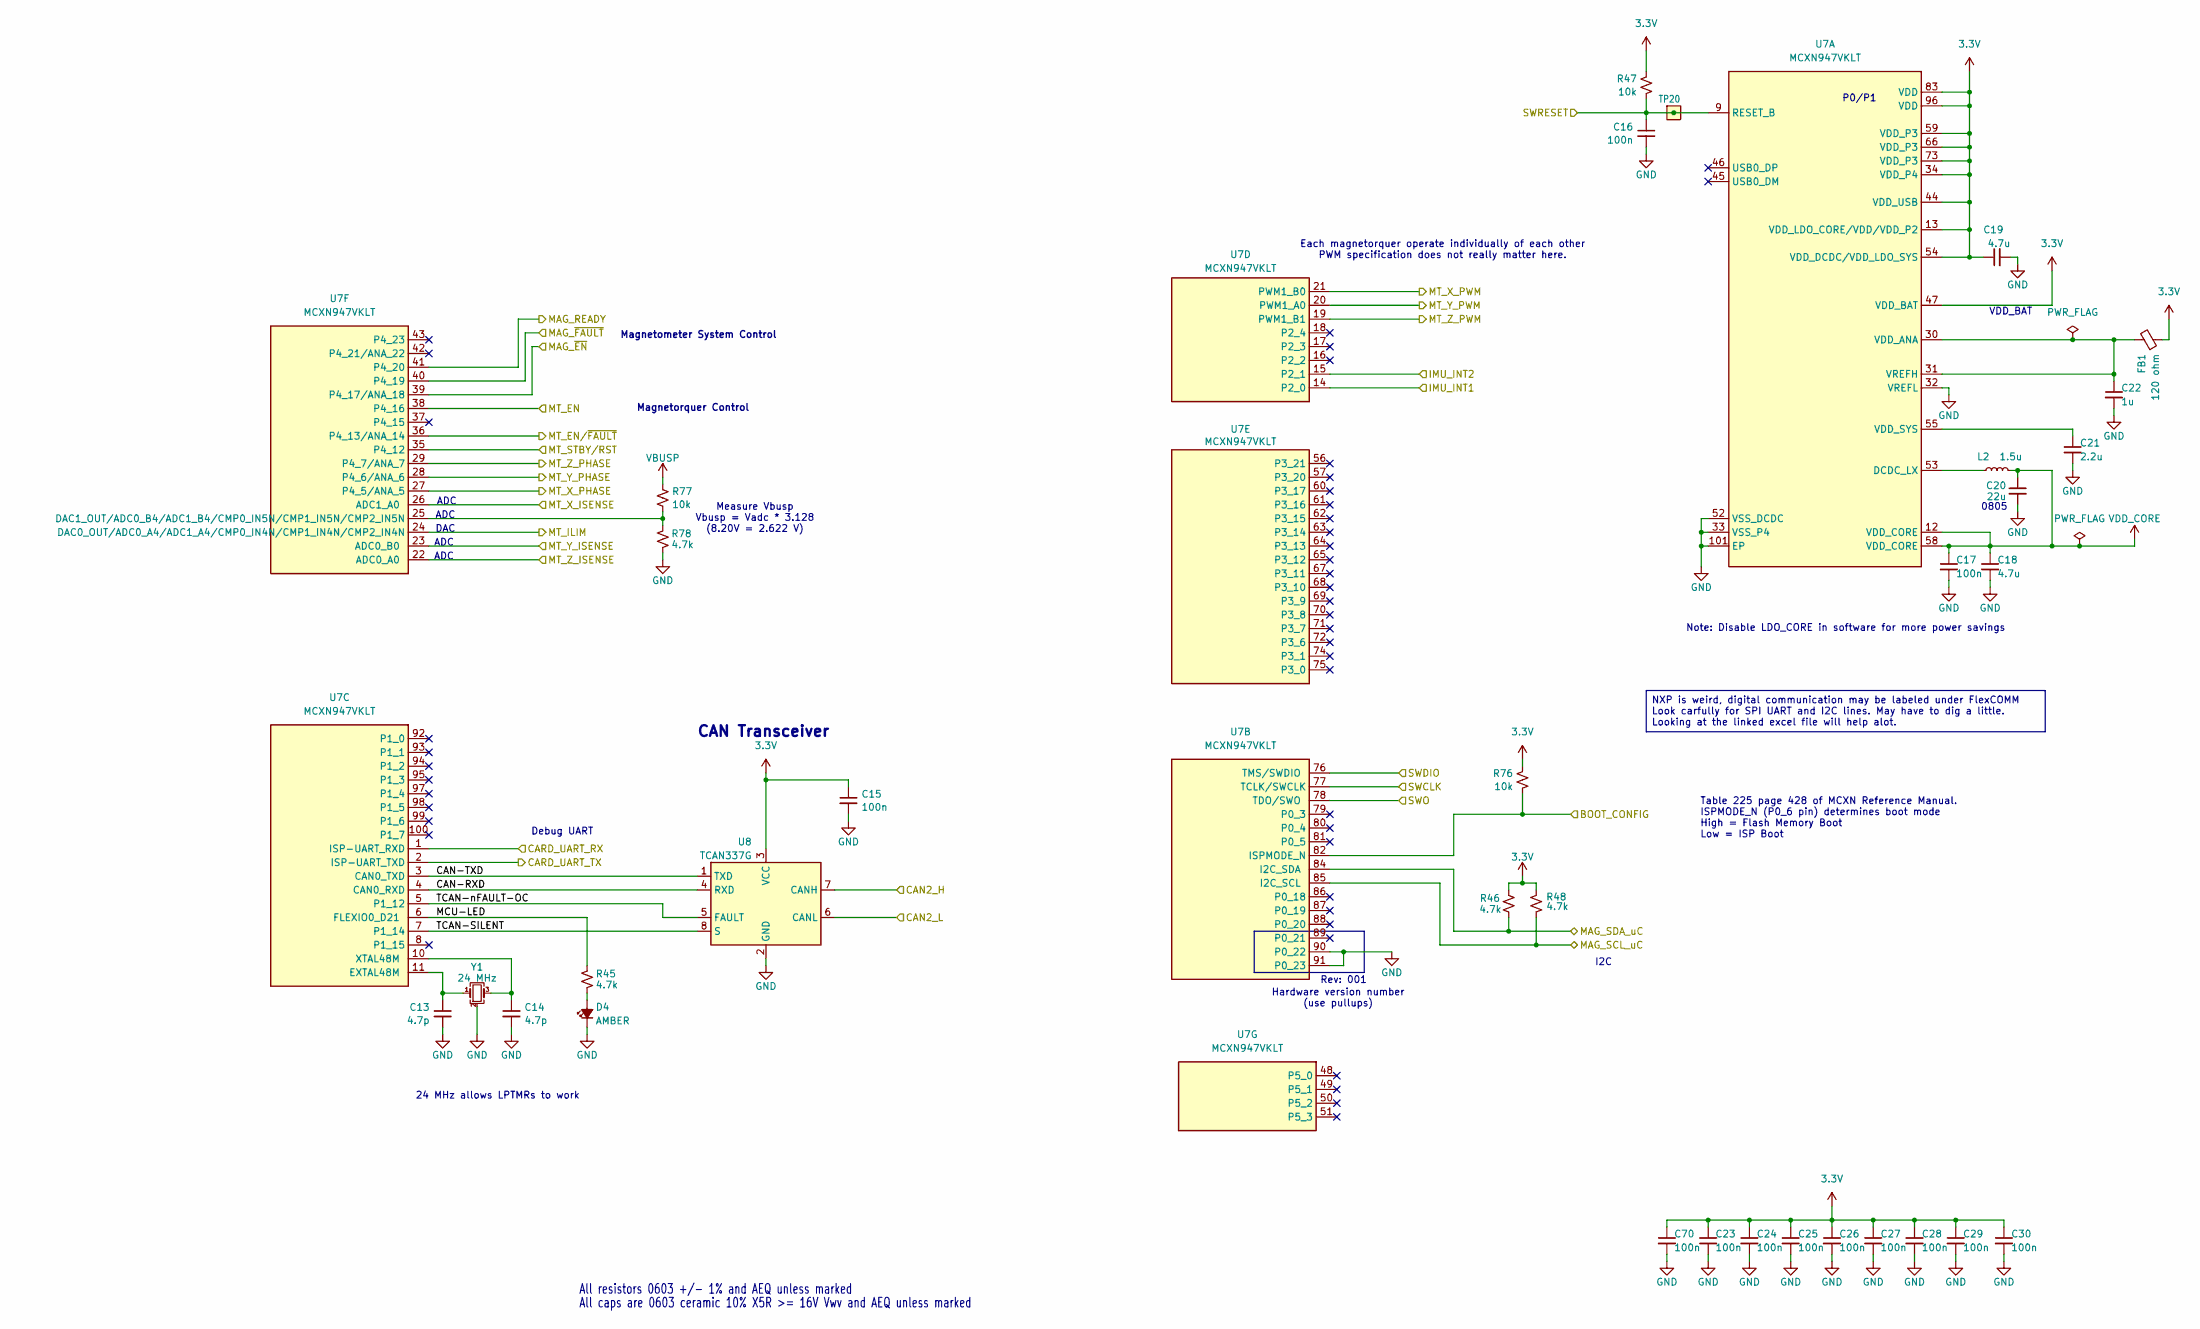
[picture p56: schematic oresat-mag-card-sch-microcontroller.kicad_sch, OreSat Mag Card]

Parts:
C13, C14: 4.7p; 0603-C-NOSILK; MPN C0603C479D5GACAUTO
C15, C16, C17, C23, C24, C25, C26, C27, C28, C29, C30, C70: 100n; 0603-C-NOSILK; MPN C0603C104K5RACAUTO
C18, C19: 4.7u; 0603-C-NOSILK; MPN GRT188C71C475KE13D
C20: 22u; 0805-B-NOSILK; MPN GRT21BC81C226ME13L
C21: 2.2u; 0603-C-NOSILK; MPN GRT188C71E225KE13D
C22: 1u; 0603-C-NOSILK; MPN GRT188R71E105KE13D
D4: AMBER; LED_0603_1608Metric; MPN 150060AS75000
FB1: 120 ohm; 0805-B-NOSILK; MPN 2508051217Y6
L2: 1.5u; L_0805_2012Metric; MPN SRP2012TMA-1R5M
R45, R46, R48, R78: 4.7k; 0603-C-NOSILK; MPN RMCF0603FT4K70
R47, R76, R77: 10k; 0603-C-NOSILK; MPN RMCF0603FT10K0
TP20: Test-Point; TestPoint-0.75mm-th
U7: MCXN947VKLT; MCXN947KVLT-QFP50P1600X1600X160-101N; MPN MCXN947VKLT
U8: TCAN337G; SOT-23-8; MPN TCAN337GDCNR
Y1: 24 MHz; Crystal_SMD_2016-4Pin_2.0x1.6mm; MPN 830108212309

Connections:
3.3V: C15.1, C19.1, C23.1, C24.1, C25.1, C26.1, C27.1, C28.1, C29.1, C30.1, C70.1, FB1.1, R46.2, R47.2, R48.2, R76.2, U7.13 (VDD_LDO_CORE/VDD/VDD_P2), U7.34 (VDD_P4), U7.44 (VDD_USB), U7.47 (VDD_BAT), U7.54 (VDD_DCDC/VDD_LDO_SYS), U7.59 (VDD_P3), U7.66 (VDD_P3), U7.73 (VDD_P3), U7.83 (VDD), U7.96 (VDD), U8.3 (VCC); also elsewhere on the board
/CAN2_H: U8.7 (CANH); also elsewhere on the board
/CAN2_L: U8.6 (CANL); also elsewhere on the board
/Card Power Domain/BOOT_CONFIG: R76.1, U7.82 (ISPMODE_N); also elsewhere on the board
/Card Power Domain/CARD-UART-RX: U7.1 (ISP-UART_RXD); also elsewhere on the board
/Card Power Domain/CARD-UART-TX: U7.2 (ISP-UART_TXD); also elsewhere on the board
/Magnetometers + IMU/IMU_INT1: U7.14 (P2_0); also elsewhere on the board
/Magnetometers + IMU/IMU_INT2: U7.15 (P2_1); also elsewhere on the board
/Magnetometers + IMU/MAG_READY: U7.41 (P4_20); also elsewhere on the board
/Magnetometers + IMU/MAG_SCL_uC: R48.1, U7.85 (I2C_SCL); also elsewhere on the board
/Magnetometers + IMU/MAG_SDA_uC: R46.1, U7.84 (I2C_SDA); also elsewhere on the board
/Magnetometers + IMU/MAG_~EN: U7.39 (P4_17/ANA_18); also elsewhere on the board
/Magnetometers + IMU/MAG_~FAULT: U7.40 (P4_19); also elsewhere on the board
/Magnetorquers/MT_EN: U7.38 (P4_16); also elsewhere on the board
/Magnetorquers/MT_EN/~FAULT: U7.36 (P4_13/ANA_14); also elsewhere on the board
/Magnetorquers/MT_ILIM: U7.24 (DAC0_OUT/ADC0_A4/ADC1_A4/CMP0_IN4N/CMP1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); also elsewhere on the board
/Magnetorquers/MT_STBY/RST: U7.35 (P4_12); also elsewhere on the board
/Magnetorquers/MT_X_ISENSE: U7.26 (ADC1_A0); also elsewhere on the board
/Magnetorquers/MT_X_PHASE: U7.27 (P4_5/ANA_5); also elsewhere on the board
/Magnetorquers/MT_X_PWM: U7.21 (PWM1_B0); also elsewhere on the board
/Magnetorquers/MT_Y_ISENSE: U7.23 (ADC0_B0); also elsewhere on the board
/Magnetorquers/MT_Y_PHASE: U7.28 (P4_6/ANA_6); also elsewhere on the board
/Magnetorquers/MT_Y_PWM: U7.20 (PWM1_A0); also elsewhere on the board
/Magnetorquers/MT_Z_ISENSE: U7.22 (ADC0_A0); also elsewhere on the board
/Magnetorquers/MT_Z_PHASE: U7.29 (P4_7/ANA_7); also elsewhere on the board
/Magnetorquers/MT_Z_PWM: U7.19 (PWM1_B1); also elsewhere on the board
/Microcontroller/CAN-RXD: U7.4 (CAN0_RXD), U8.4 (RXD)
/Microcontroller/CAN-TXD: U7.3 (CAN0_TXD), U8.1 (TXD)
/Microcontroller/MCU-LED: R45.1, U7.6 (FLEXIO0_D21)
/Microcontroller/TCAN-SILENT: U7.7 (P1_14), U8.8 (S)
/Microcontroller/TCAN-nFAULT-OC: U7.5 (P1_12), U8.5 (FAULT)
/NRST: C16.1, R47.1, TP20.1 (1_1), U7.9 (RESET_B); also elsewhere on the board
/SWCLK: U7.77 (TCLK/SWCLK); also elsewhere on the board
/SWDIO: U7.76 (TMS/SWDIO); also elsewhere on the board
/SWO: U7.78 (TDO/SWO); also elsewhere on the board
GND: C13.2, C14.2, C15.2, C16.2, C17.2, C18.2, C19.2, C20.2, C21.2, C22.2, C23.2, C24.2, C25.2, C26.2, C27.2, C28.2, C29.2, C30.2, C70.2, D4.1 (K), R78.2, U7.32 (VREFL), U7.33 (VSS_P4), U7.52 (VSS_DCDC), U7.90 (P0_22), U7.91 (P0_23), U7.101 (EP), U8.2 (GND), Y1.2 (G), Y1.4 (G); also elsewhere on the board
unnamed: D4.2 (A), R45.2
unnamed: L2.2, U7.53 (DCDC_LX)
unnamed: C22.1, FB1.2, U7.30 (VDD_ANA), U7.31 (VREFH)
unnamed: C21.1, U7.55 (VDD_SYS)
unnamed: C14.1, U7.10 (XTAL48M), Y1.3
unnamed: C13.1, U7.11 (EXTAL48M), Y1.1
unnamed: R77.1, R78.1, U7.25 (DAC1_OUT/ADC0_B4/ADC1_B4/CMP0_IN5N/CMP1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)
VBUSP: R77.2; also elsewhere on the board
VDD_CORE: C17.1, C18.1, C20.1, L2.1, U7.12 (VDD_CORE), U7.58 (VDD_CORE)

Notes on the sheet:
Magnetometer System Control
Measure Vbusp Vbusp = Vadc * 3.128 (8.20V = 2.622 V)
Hardware version number (use pullups)
ADC
Magnetorquer Control
Each magnetorquer operate individually of each other PWM specification does not really matter here.
Debug UART
Note: Disable LDO_CORE in software for more power savings
0805
All resistors 0603 +/- 1% and AEQ unless marked
I2C
VDD_BAT
Table 225 page 428 of MCXN Reference Manual. ISPMODE_N (P0_6 pin) determines boot mode High = Flash Memory Boot Low = ISP Boot
CAN Transceiver
All caps are 0603 ceramic 10% X5R >= 16V Vwv and AEQ unless marked
24 MHz allows LPTMRs to work
P0/P1
DAC
Rev: 001
NXP is weird, digital communication may be labeled under FlexCOMM Look carfully for SPI UART and I2C lines. May have to dig a little. Looking at the linked excel file will help alot.

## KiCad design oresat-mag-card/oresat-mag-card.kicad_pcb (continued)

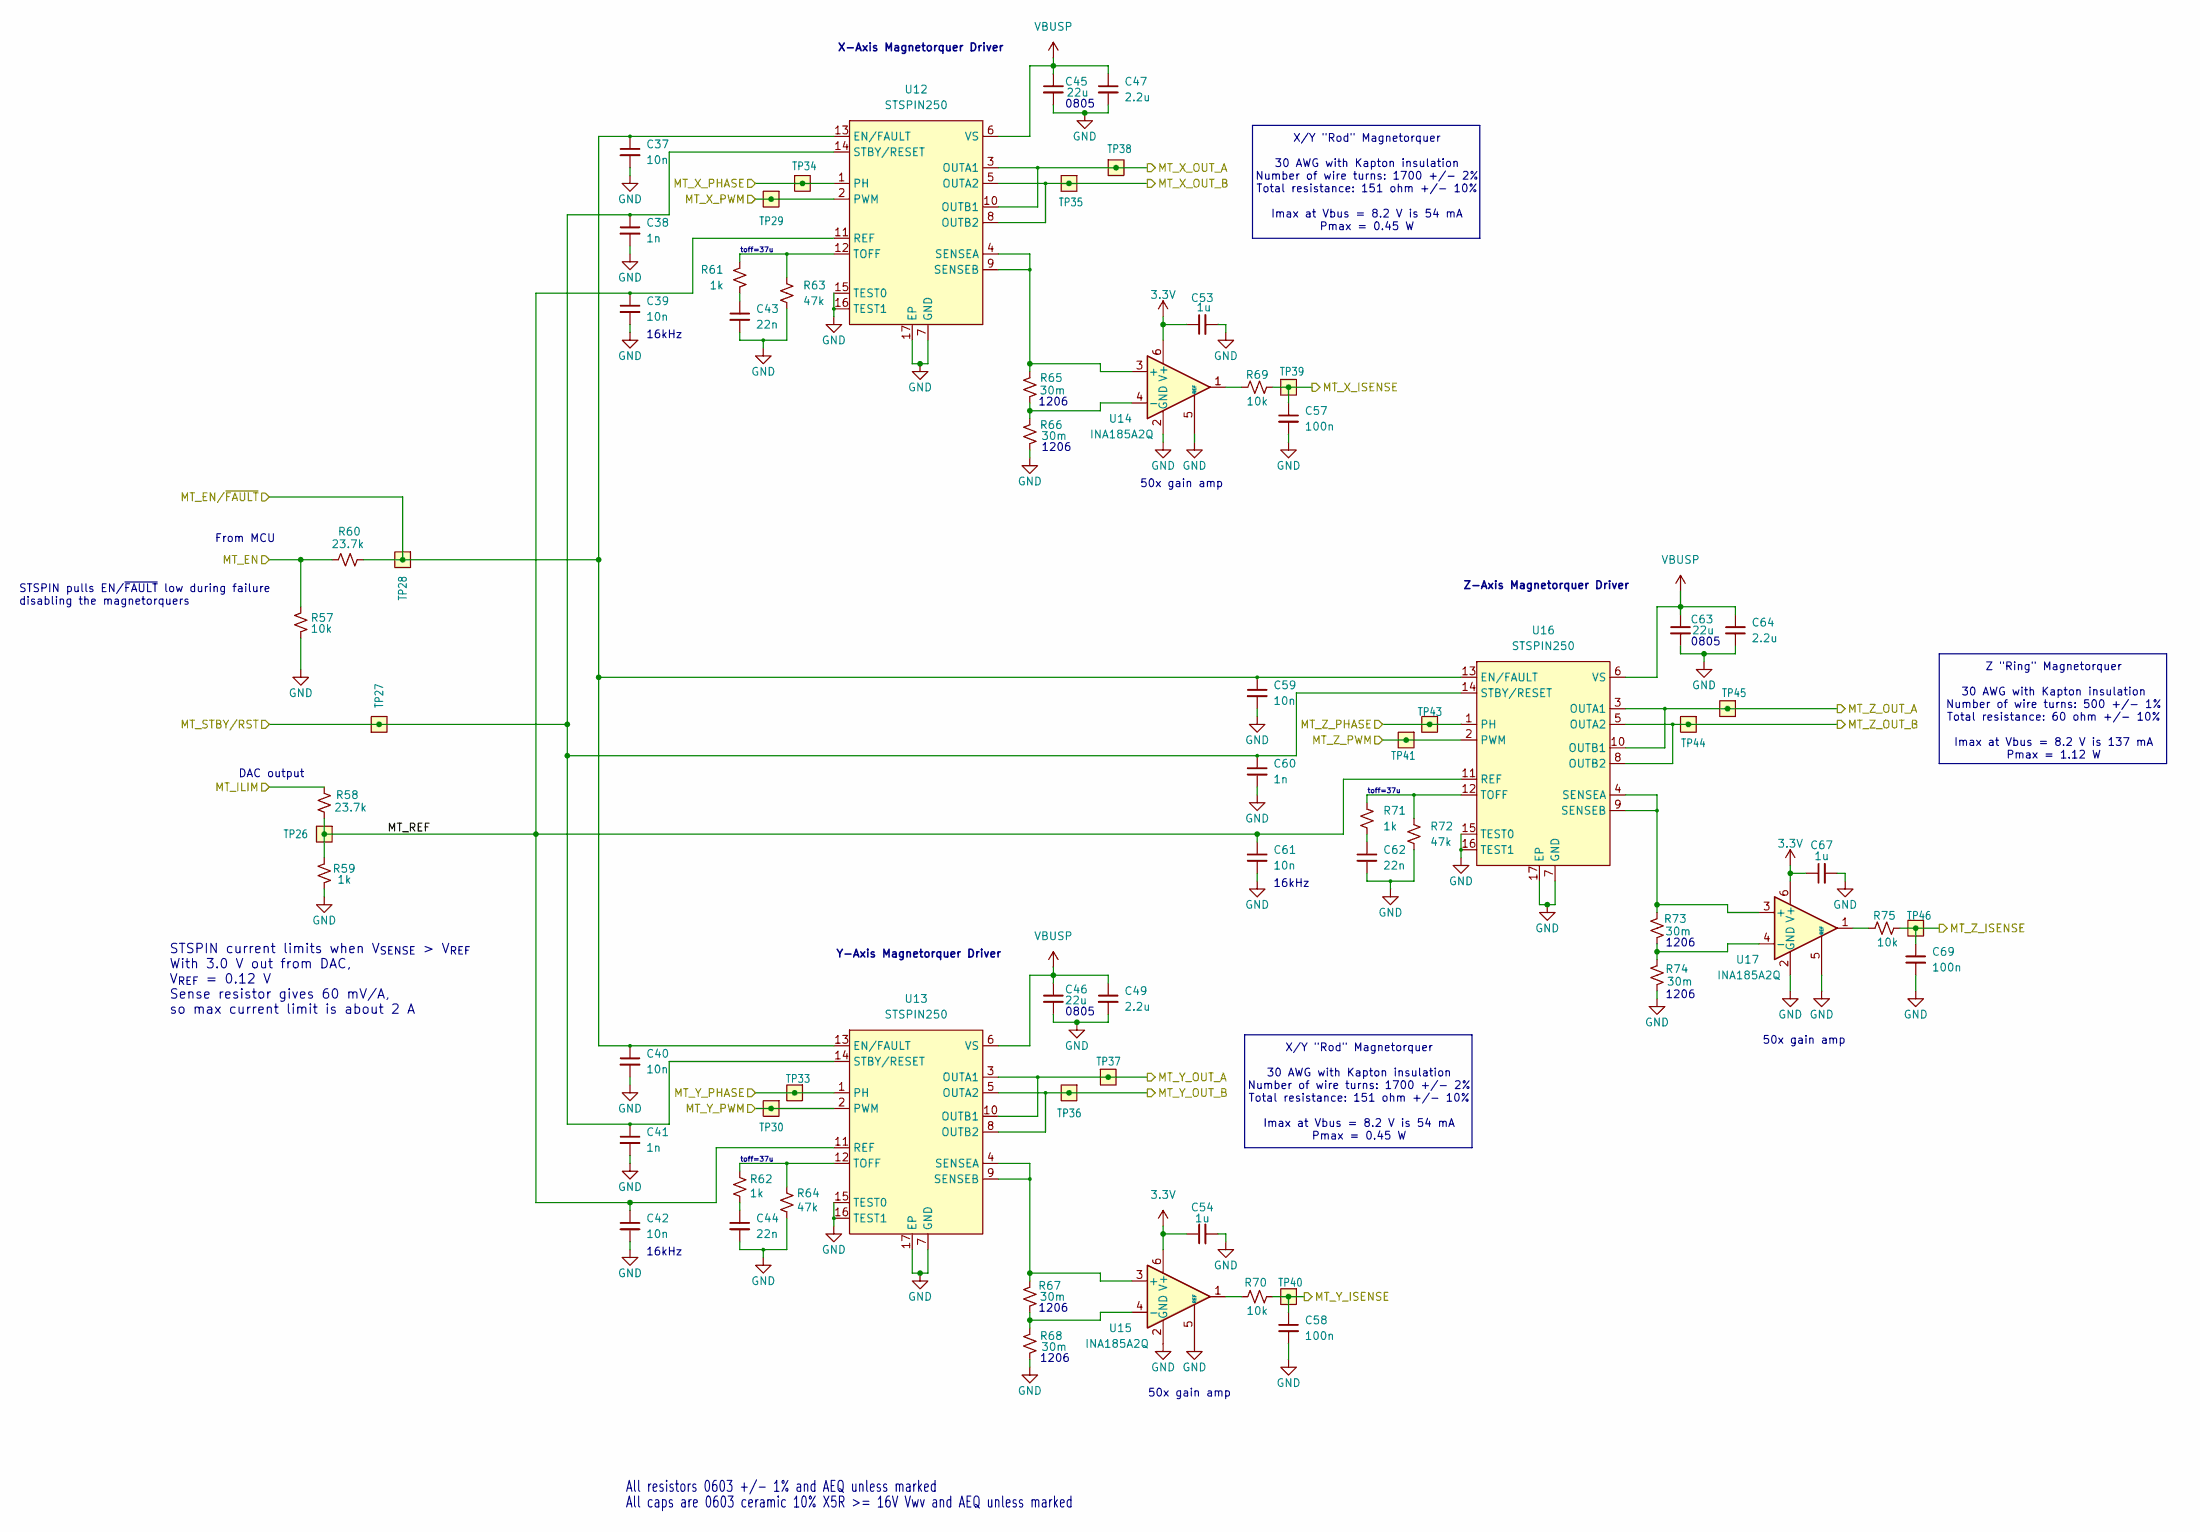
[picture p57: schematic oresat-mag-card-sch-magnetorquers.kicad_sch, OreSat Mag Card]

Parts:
C37, C39, C40, C42, C59, C61: 10n; 0603-C-NOSILK; MPN C0603C103J5RACAUTO
C38, C41, C60: 1n; 0603-C-NOSILK; MPN C0603C102J5RACAUTO
C43, C44, C62: 22n; 0603-C-NOSILK; MPN C0603C223J5RACAUTO
C45, C46, C63: 22u; 0805-B-NOSILK; MPN GRT21BC81C226ME13L
C47, C49, C64: 2.2u; 0603-C-NOSILK; MPN GRT188C71E225KE13D
C53, C54, C67: 1u; 0603-C-NOSILK; MPN GRT188R71E105KE13D
C57, C58, C69: 100n; 0603-C-NOSILK; MPN C0603C104K5RACAUTO
R57, R69, R70, R75: 10k; 0603-C-NOSILK; MPN RMCF0603FT10K0
R58, R60: 23.7k; 0603-C-NOSILK; MPN RMCF0603FT23K7
R59, R61, R62, R71: 1k; 0603-C-NOSILK; MPN RMCF0603FT1K00
R63, R64, R72: 47k; 0603-C-NOSILK; MPN RMCF0603FT47K0
R65, R66, R67, R68, R73, R74: 30m; 1206-C; MPN CSR1206FK30L0
TP26, TP27, TP28, TP29, TP30, TP33, TP34, TP35, TP36, TP37, TP38, TP39, TP40, TP41, TP43, TP44, TP45, TP46: Test-Point; TestPoint-0.75mm-th
U12, U13, U16: STSPIN250; VQFN-16-1EP_3x3mm_P0.5mm_EP1.8x1.8mm; MPN STSPIN250
U14, U15, U17: INA185A2Q; SOT-363_SC-70-6; MPN INA185A2QDCKRQ1

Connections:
3.3V: C53.1, C54.1, C67.1, U14.6 (V+), U15.6 (V+), U17.6 (V+); also elsewhere on the board
/MT_X_OUT_A: TP38.1 (1_1), U12.3 (OUTA1), U12.10 (OUTB1); also elsewhere on the board
/MT_X_OUT_B: TP35.1 (1_1), U12.5 (OUTA2), U12.8 (OUTB2); also elsewhere on the board
/MT_Y_OUT_A: TP37.1 (1_1), U13.3 (OUTA1), U13.10 (OUTB1); also elsewhere on the board
/MT_Y_OUT_B: TP36.1 (1_1), U13.5 (OUTA2), U13.8 (OUTB2); also elsewhere on the board
/MT_Z_OUT_A: TP45.1 (1_1), U16.3 (OUTA1), U16.10 (OUTB1); also elsewhere on the board
/MT_Z_OUT_B: TP44.1 (1_1), U16.5 (OUTA2), U16.8 (OUTB2); also elsewhere on the board
/Magnetorquers/MT_EN: R57.2, R60.1; also elsewhere on the board
/Magnetorquers/MT_EN/~FAULT: C37.1, C40.1, C59.1, R60.2, TP28.1 (1_1), U12.13 (EN/FAULT), U13.13 (EN/FAULT), U16.13 (EN/FAULT); also elsewhere on the board
/Magnetorquers/MT_ILIM: R58.2; also elsewhere on the board
/Magnetorquers/MT_REF: C39.1, C42.1, C61.1, R58.1, R59.2, TP26.1 (1_1), U12.11 (REF), U13.11 (REF), U16.11 (REF)
/Magnetorquers/MT_STBY/RST: C38.1, C41.1, C60.1, TP27.1 (1_1), U12.14 (STBY/RESET), U13.14 (STBY/RESET), U16.14 (STBY/RESET); also elsewhere on the board
/Magnetorquers/MT_X_ISENSE: C57.1, R69.2, TP39.1 (1_1); also elsewhere on the board
/Magnetorquers/MT_X_PHASE: TP34.1 (1_1), U12.1 (PH); also elsewhere on the board
/Magnetorquers/MT_X_PWM: TP29.1 (1_1), U12.2 (PWM); also elsewhere on the board
/Magnetorquers/MT_Y_ISENSE: C58.1, R70.2, TP40.1 (1_1); also elsewhere on the board
/Magnetorquers/MT_Y_PHASE: TP33.1 (1_1), U13.1 (PH); also elsewhere on the board
/Magnetorquers/MT_Y_PWM: TP30.1 (1_1), U13.2 (PWM); also elsewhere on the board
/Magnetorquers/MT_Z_ISENSE: C69.1, R75.2, TP46.1 (1_1); also elsewhere on the board
/Magnetorquers/MT_Z_PHASE: TP43.1 (1_1), U16.1 (PH); also elsewhere on the board
/Magnetorquers/MT_Z_PWM: TP41.1 (1_1), U16.2 (PWM); also elsewhere on the board
GND: C37.2, C38.2, C39.2, C40.2, C41.2, C42.2, C43.2, C44.2, C45.2, C46.2, C47.2, C49.2, C53.2, C54.2, C57.2, C58.2, C59.2, C60.2, C61.2, C62.2, C63.2, C64.2, C67.2, C69.2, R57.1, R59.1, R63.2, R64.2, R66.1, R68.1, R72.2, R74.1, U12.7 (GND), U12.15 (TEST0), U12.16 (TEST1), U12.17 (EP), U13.7 (GND), U13.15 (TEST0), U13.16 (TEST1), U13.17 (EP), U14.2 (GND), U14.5 (REF), U15.2 (GND), U15.5 (REF), U16.7 (GND), U16.15 (TEST0), U16.16 (TEST1), U16.17 (EP), U17.2 (GND), U17.5 (REF); also elsewhere on the board
unnamed: C43.1, R61.2
unnamed: C44.1, R62.2
unnamed: C62.1, R71.2
unnamed: R69.1, U14.1
unnamed: R70.1, U15.1
unnamed: R75.1, U17.1
unnamed: R65.2, U12.4 (SENSEA), U12.9 (SENSEB), U14.3 (+)
unnamed: R61.1, R63.1, U12.12 (TOFF)
unnamed: R67.2, U13.4 (SENSEA), U13.9 (SENSEB), U15.3 (+)
unnamed: R62.1, R64.1, U13.12 (TOFF)
unnamed: R65.1, R66.2, U14.4 (-)
unnamed: R67.1, R68.2, U15.4 (-)
unnamed: R73.2, U16.4 (SENSEA), U16.9 (SENSEB), U17.3 (+)
unnamed: R71.1, R72.1, U16.12 (TOFF)
unnamed: R73.1, R74.2, U17.4 (-)
VBUSP: C45.1, C46.1, C47.1, C49.1, C63.1, C64.1, U12.6 (VS), U13.6 (VS), U16.6 (VS); also elsewhere on the board

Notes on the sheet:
1206
STSPIN current limits when V_{SENSE} > V_{REF} With 3.0 V out from DAC, V_{REF} = 0.12 V Sense resistor gives 60 mV/A, so max current limit is about 2 A
DAC output
16kHz
50x gain amp
toff=37u
Y-Axis Magnetorquer Driver
X/Y "Rod" Magnetorquer 30 AWG with Kapton insulation Number of wire turns: 1700 +/- 2% Total resistance: 151 ohm +/- 10% Imax at Vbus = 8.2 V is 54 mA Pmax = 0.45 W
From MCU
All caps are 0603 ceramic 10% X5R >= 16V Vwv and AEQ unless marked
Z "Ring" Magnetorquer 30 AWG with Kapton insulation Number of wire turns: 500 +/- 1% Total resistance: 60 ohm +/- 10% Imax at Vbus = 8.2 V is 137 mA Pmax = 1.12 W
0805
STSPIN pulls EN/~{FAULT} low during failure disabling the magnetorquers
All resistors 0603 +/- 1% and AEQ unless marked
Z-Axis Magnetorquer Driver
X-Axis Magnetorquer Driver

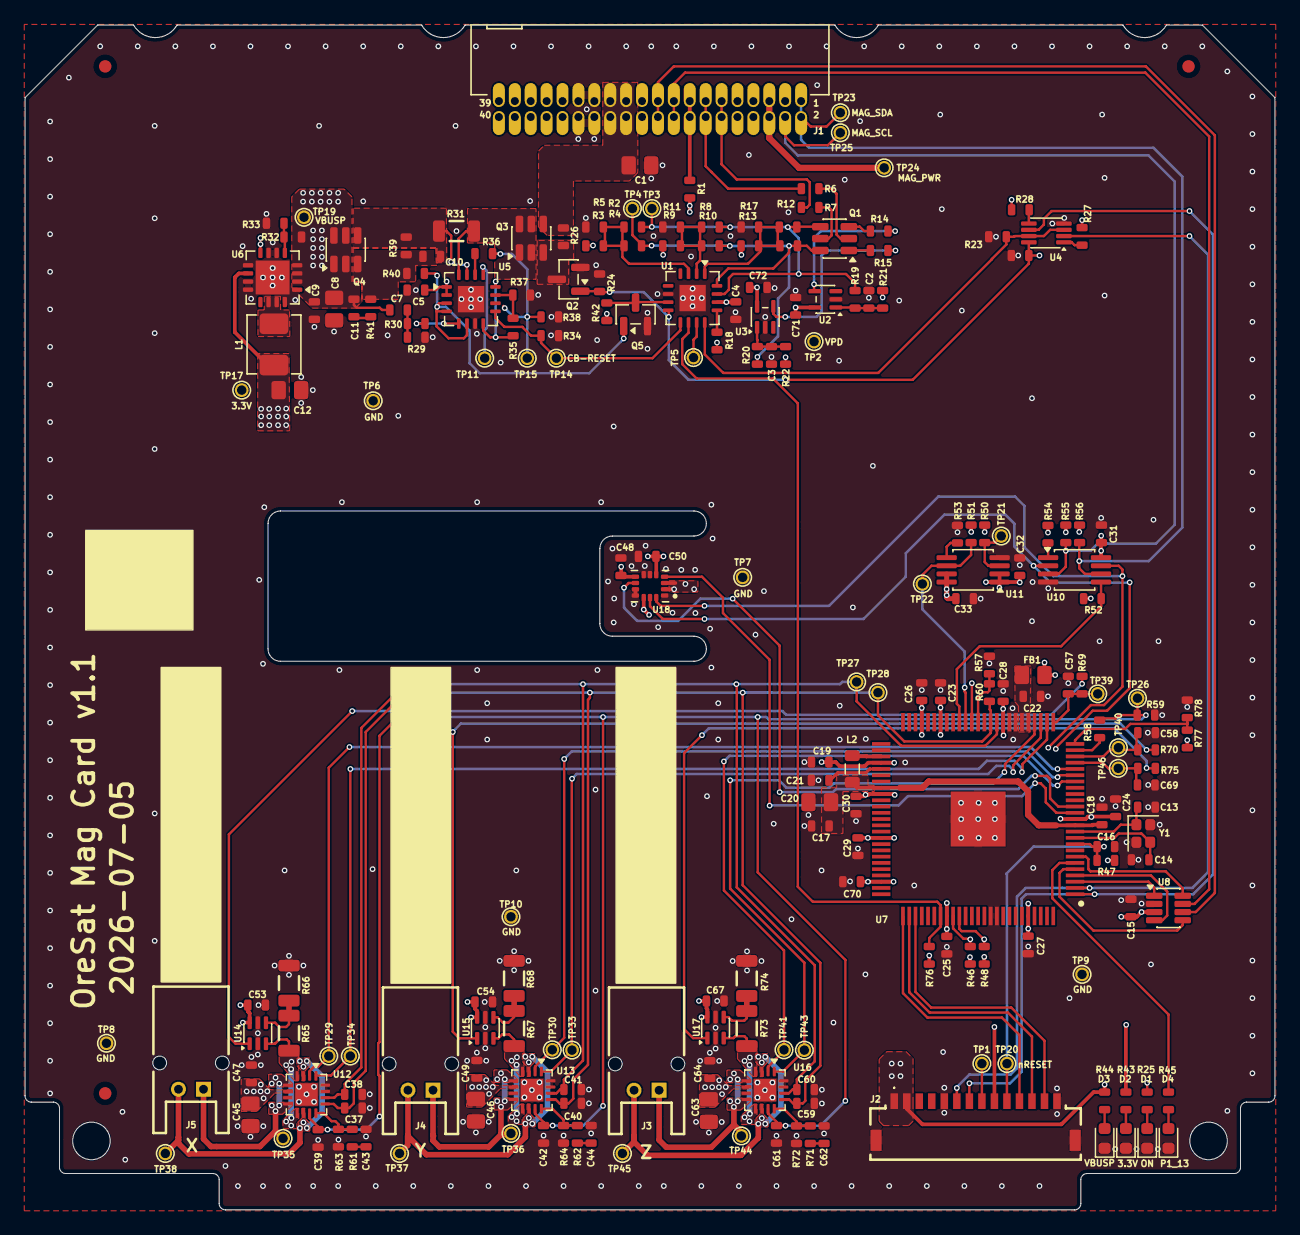
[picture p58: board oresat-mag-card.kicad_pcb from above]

Board: 4 copper layers, 99.8 x 94.6 mm, 217 parts (0 on the bottom side), 119 nets.

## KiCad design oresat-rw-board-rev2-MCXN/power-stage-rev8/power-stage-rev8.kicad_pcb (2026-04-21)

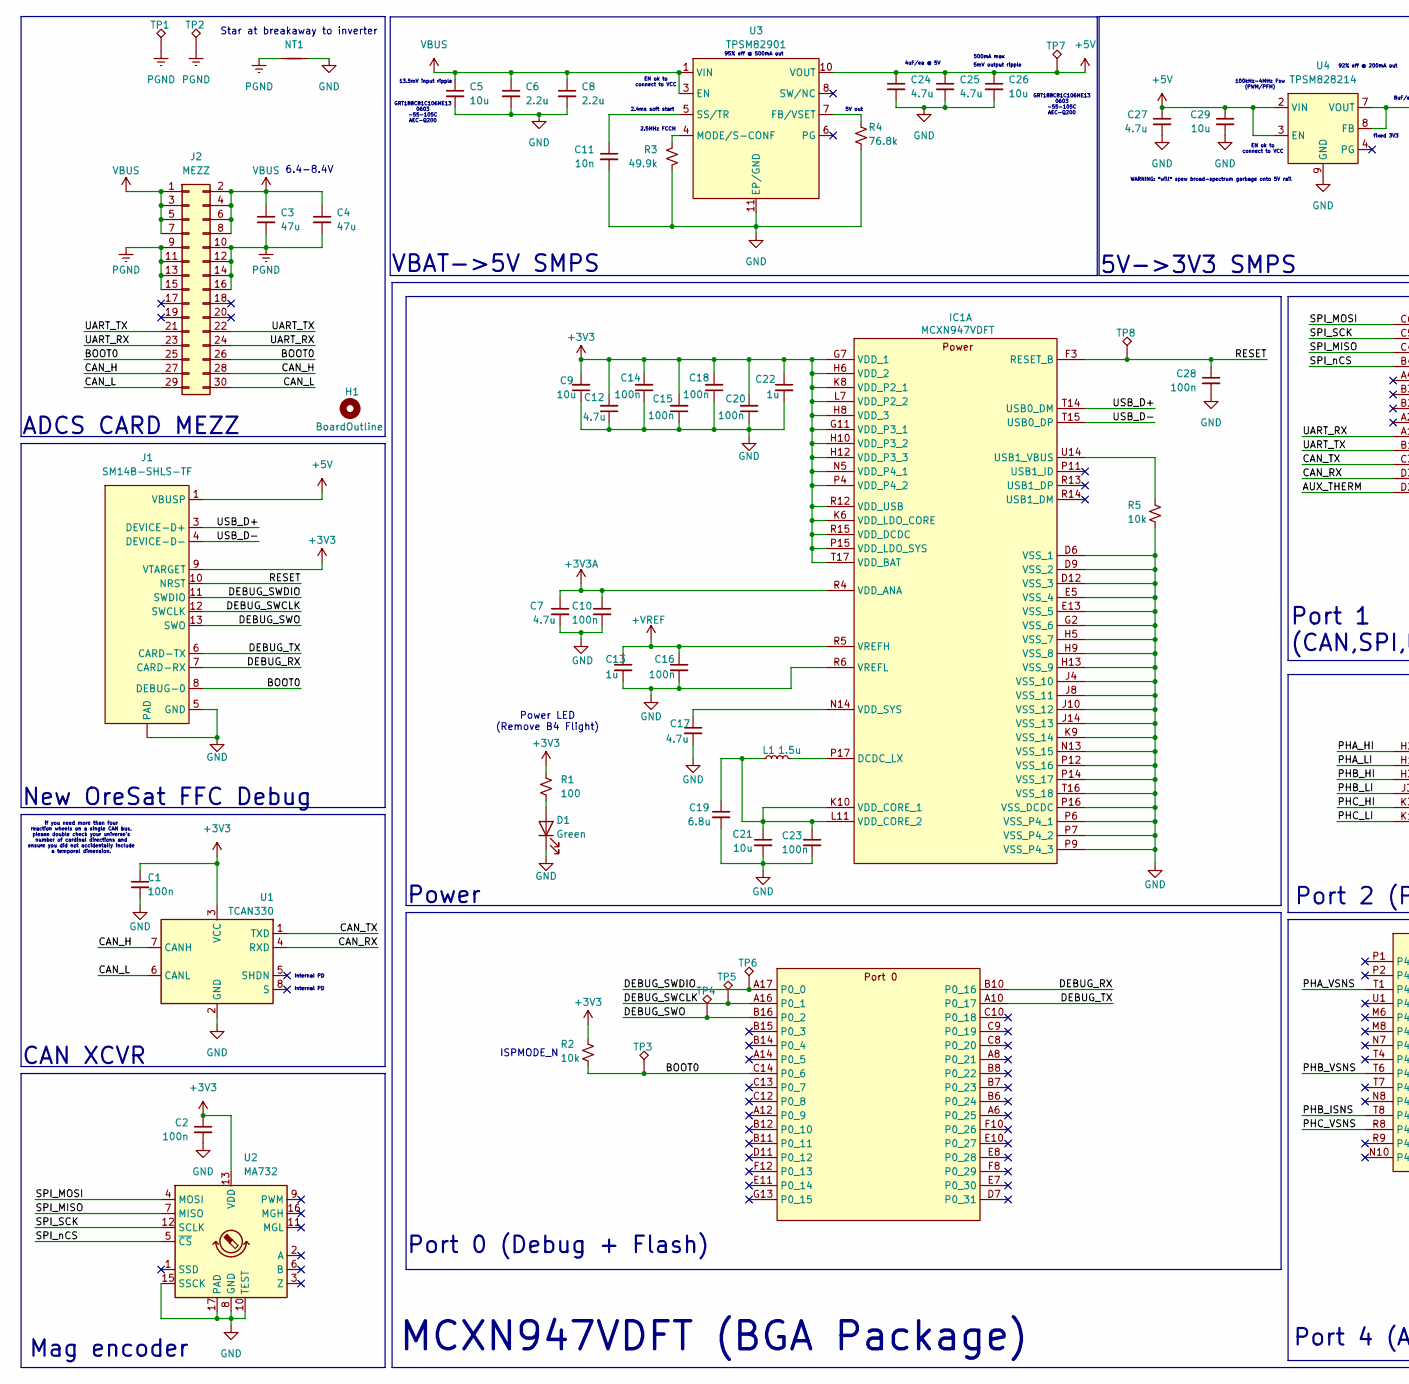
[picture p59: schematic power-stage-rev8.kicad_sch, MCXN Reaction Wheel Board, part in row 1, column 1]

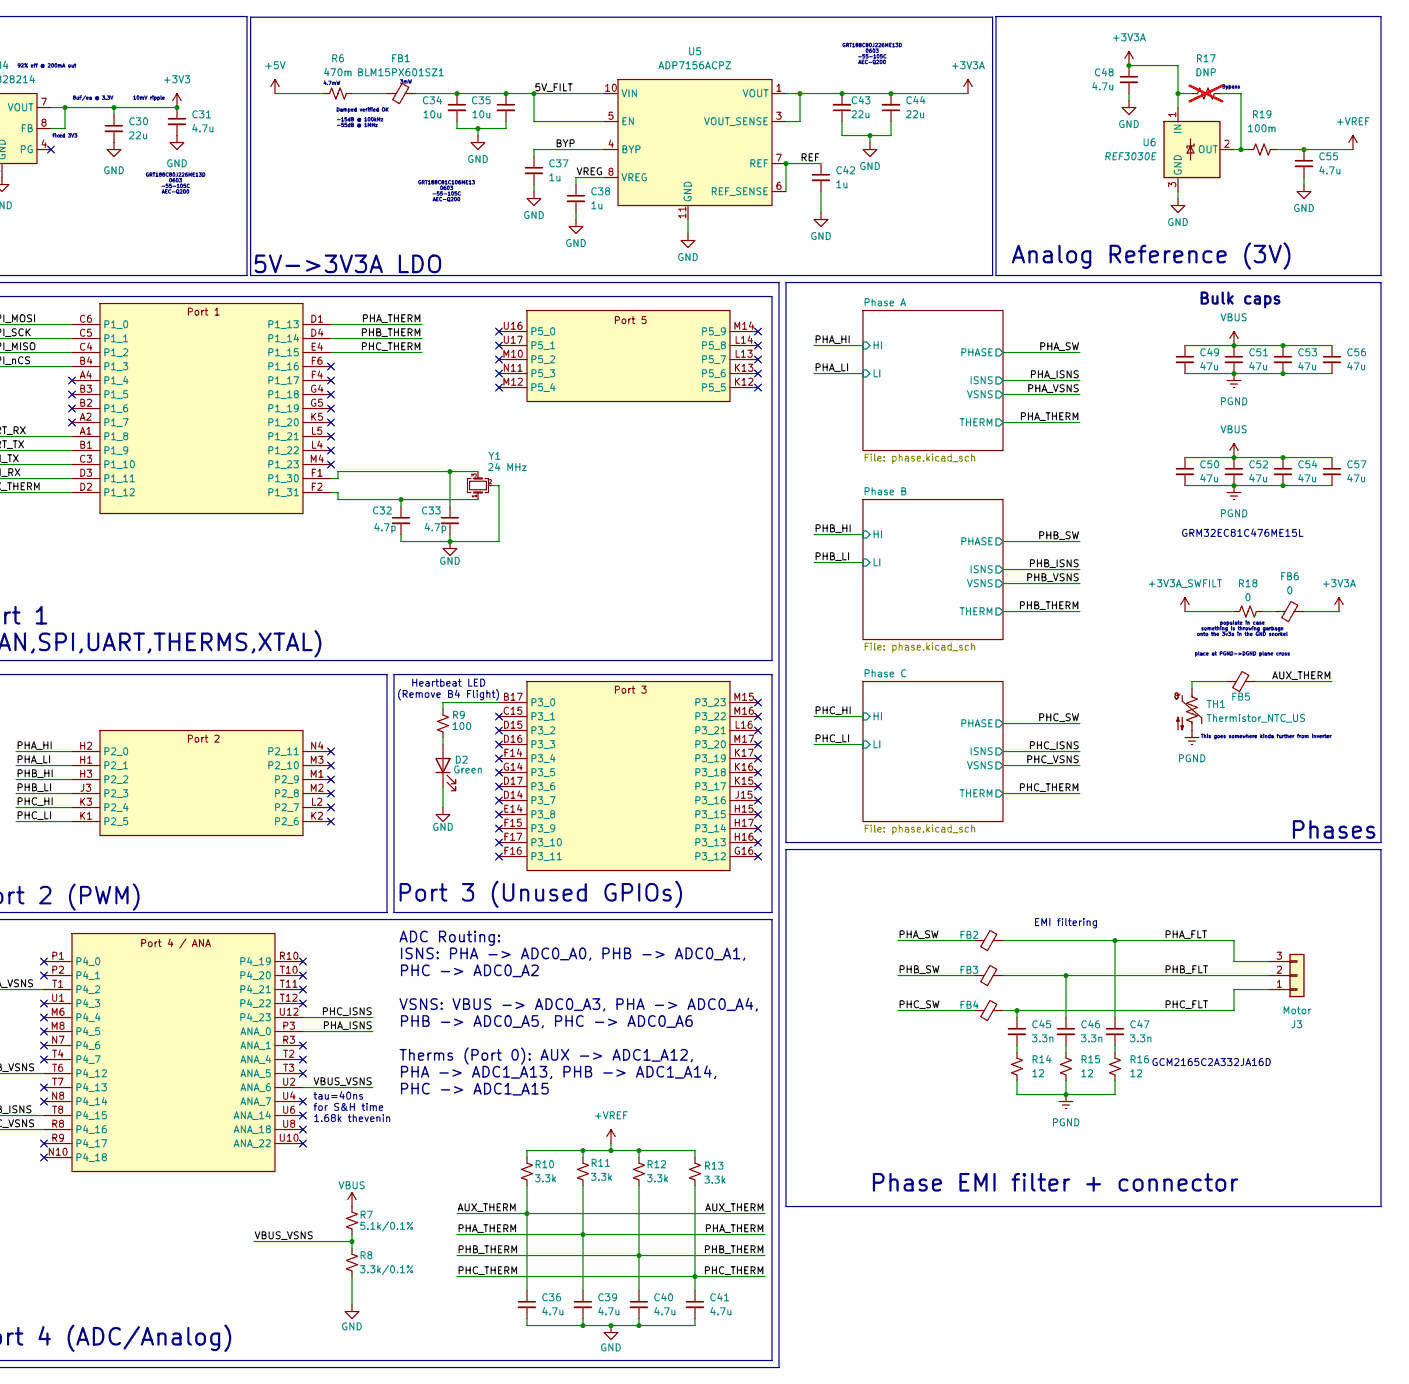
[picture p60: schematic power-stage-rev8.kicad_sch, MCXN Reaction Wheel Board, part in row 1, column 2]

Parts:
C1, C2, C10, C14, C15, C16, C18, C20, C23, C28: 100n; C_0402_1005Metric; MPN GRT155R71E104KE01J
C3, C4, C49, C50, C51, C52, C53, C54, C56, C57: 47u; C_1210_3225Metric; MPN GRT32EC81C476KE13L
C5, C9, C21, C26, C29, C34, C35: 10u; C_0603_1608Metric; MPN GRT188C81C106ME13D
C6, C8: 2.2u; C_0402_1005Metric; MPN GRT155C81C225ME13D
C7, C12, C17, C24, C25, C27, C31, C36, C39, C40, C41, C48, C55: 4.7u; C_0402_1005Metric; MPN GRT155C81A475ME13J
C11: 10n; C_0402_1005Metric; MPN GCM155R71H103KA55D
C13, C22, C37, C38, C42: 1u; C_0402_1005Metric; MPN GRT155C81A105ME01D
C19: 6.8u; C_1206_3216Metric; MPN CGA5L1X7R1C685M160AC
C30, C43, C44: 22u; C_0603_1608Metric; MPN GRT188C80J226ME13D
C32, C33: 4.7p; C_0603_1608Metric; MPN GRM1885C1H4R7WA01D
C45, C46, C47: 3.3n; C_0805_2012Metric; MPN GCM2165C2A332JA16D
D1, D2: Green; LED_0603_1608Metric; MPN 150060VS55040
FB1, FB5: BLM15PX601SZ1; L_0402_1005Metric; MPN BLM15PX601SZ1D
FB2, FB3, FB4: BLM31SN500SN1L; L_1206_3216Metric; MPN BLM31SN500SN1L
FB6: 0; L_0402_1005Metric; MPN AC0402FR-070RL
H1: BoardOutline; board_def_rev8.0
IC1: MCXN947VDFT; BGA184C50P17X17_900X900X98; Manufacturer_Part_Number MCXN947VDFT
J1: SM14B-SHLS-TF; J-JST-SM14BSHLSTF; MPN SM14B-SHLS-TF
J2: MEZZ; 0555600307; MPN 0555600307
J3: Motor; Molex_Micro-Fit_3.0_43650-0315_1x03_P3.00mm_Vertical
L1: 1.5u; L_0805_2012Metric; MPN SRP2012TMA-1R5M
NT1: NetTie_2; NetTie-2_SMD_Pad2.0mm
R1, R9: 100; R_0402_1005Metric; MPN SR0402FR-7T100RL
R2, R5: 10k; R_0402_1005Metric; MPN AC0402DR-0710KL
R3: 49.9k; R_0402_1005Metric; MPN AC0402FR-0749K9L
R4: 76.8k; R_0402_1005Metric; MPN AC0402FR-0776K8L
R6: 470m; R_0402_1005Metric; MPN PE0402FRF7W0R47L
R7: 5.1k/0.1%; R_0402_1005Metric; MPN RP0402BRD075K1L
R8: 3.3k/0.1%; R_0402_1005Metric; MPN RP0402BRD073K3L
R10, R11, R12, R13: 3.3k; R_0402_1005Metric; MPN AC0402FR-073K3L
R14, R15, R16: 12; R_0805_2012Metric; MPN SR0805FR-7T12RL
R17: DNP; R_0402_1005Metric; MPN AC0402FR-070RL; not fitted
R18: 0; R_0402_1005Metric; MPN AC0402FR-070RL
R19: 100m; R_0402_1005Metric; MPN PE0402FRF470R1L
TH1: Thermistor_NTC_US; R_0402_1005Metric; MPN NCU15XH103F6SRC
TP1, TP2, TP3, TP4, TP5, TP6, TP7, TP8: TestPoint_Alt; TestPoint_Pad_1.0x1.0mm_NoSilk
U1: TCAN330; SOT-23-8; MPN TCAN330DCNR
U2: MA732; QFN-16-1EP_3x3mm_P0.5mm_EP1.75x1.75mm; MPN MA732GQ-Z
U3: TPSM82901; TI_uSIP_SIS; MPN TPSM82901SISR
U4: TPSM828214; TI_uSIP_SIL; MPN TPSM828214SILR
U5: ADP7156ACPZ; DFN-10-1EP_3x3mm_P0.5mm_EP1.65x2.38mm; MPN ADP7156ACPZ-3.3-R7
U6: REF3030E; SOT-23; MPN REF3030AIDBZT
Y1: 24 MHz; Crystal_SMD_2016-4Pin_2.0x1.6mm; MPN 830108212309

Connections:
+3V3: C1.1, C2.1, C9.2, C12.2, C14.2, C15.2, C18.2, C20.2, C22.1, C30.1, C31.1, IC1.G7 (VDD_1), IC1.G11 (VDD_P3_1), IC1.H6 (VDD_2), IC1.H8 (VDD_3), IC1.H10 (VDD_P3_2), IC1.H12 (VDD_P3_3), IC1.K6 (VDD_LDO_CORE), IC1.K8 (VDD_P2_1), IC1.L7 (VDD_P2_2), IC1.N5 (VDD_P4_1), IC1.P4 (VDD_P4_2), IC1.P15 (VDD_LDO_SYS), IC1.R12 (VDD_USB), IC1.R15 (VDD_DCDC), IC1.T17 (VDD_BAT), J1.9 (VTARGET), R1.1, R2.1, U1.3 (VCC), U2.13 (VDD), U4.5 (VOUT), U4.6 (VOUT), U4.7 (VOUT), U4.8 (FB)
+3V3A: C7.1, C10.1, C43.2, C44.2, C48.1, FB6.2, IC1.R4 (VDD_ANA), R17.1, U5.1 (VOUT), U5.2 (VOUT), U5.3 (VOUT_SENSE), U6.1 (IN)
+3V3A_SWFILT: R18.1; also elsewhere on the board
+5V: C24.1, C25.1, C26.1, C27.1, C29.1, J1.1 (VBUSP), J1.2 (VBUSP), R6.1, TP7.1 (1_1), U3.9 (VOUT), U3.10 (VOUT), U4.1 (VIN), U4.2 (VIN), U4.3 (EN); also elsewhere on the board
+VREF: C13.1, C16.1, C55.1, IC1.R5 (VREFH), R10.1, R11.1, R12.1, R13.1, R19.2; also elsewhere on the board
/5V_FILT: C34.1, C35.1, FB1.2, U5.5 (EN), U5.9 (VIN), U5.10 (VIN)
/AUX_THERM: C36.1, FB5.2, IC1.D2 (P1_12), R10.2
/BOOT0: IC1.C14 (P0_6), J1.8 (DEBUG-0), J2.25, J2.26, R2.2, TP3.1 (1_1)
/BYP: C37.1, U5.4 (BYP)
/CAN_H: J2.27, J2.28, U1.7 (CANH)
/CAN_L: J2.29, J2.30, U1.6 (CANL)
/CAN_RX: IC1.D3 (P1_11), U1.4 (RXD)
/CAN_TX: IC1.C3 (P1_10), U1.1 (TXD)
/DEBUG_RX: IC1.B10 (P0_16), J1.7 (CARD-RX)
/DEBUG_SWCLK: IC1.A16 (P0_1), J1.12 (SWCLK), TP5.1 (1_1)
/DEBUG_SWDIO: IC1.A17 (P0_0), J1.11 (SWDIO), TP6.1 (1_1)
/DEBUG_SWO: IC1.B16 (P0_2), J1.13 (SWO), TP4.1 (1_1)
/DEBUG_TX: IC1.A10 (P0_17), J1.6 (CARD-TX)
/PHA_FLT: C47.1, FB2.2, J3.3
/PHA_HI: IC1.H2 (P2_0); also elsewhere on the board
/PHA_ISNS: IC1.P3 (ANA_0); also elsewhere on the board
/PHA_LI: IC1.H1 (P2_1); also elsewhere on the board
/PHA_SW: FB2.1; also elsewhere on the board
/PHA_THERM: C39.1, IC1.D1 (P1_13), R11.2; also elsewhere on the board
/PHA_VSNS: IC1.T1 (P4_2); also elsewhere on the board
/PHB_FLT: C46.1, FB3.2, J3.2
/PHB_HI: IC1.H3 (P2_2); also elsewhere on the board
/PHB_ISNS: IC1.T8 (P4_15); also elsewhere on the board
/PHB_LI: IC1.J3 (P2_3); also elsewhere on the board
/PHB_SW: FB3.1; also elsewhere on the board
/PHB_THERM: C40.1, IC1.D4 (P1_14), R12.2; also elsewhere on the board
/PHB_VSNS: IC1.T6 (P4_12); also elsewhere on the board
/PHC_FLT: C45.1, FB4.2, J3.1
/PHC_HI: IC1.K3 (P2_4); also elsewhere on the board
/PHC_ISNS: IC1.U12 (P4_23); also elsewhere on the board
/PHC_LI: IC1.K1 (P2_5); also elsewhere on the board
/PHC_SW: FB4.1; also elsewhere on the board
/PHC_THERM: C41.1, IC1.E4 (P1_15), R13.2; also elsewhere on the board
/PHC_VSNS: IC1.R8 (P4_16); also elsewhere on the board
/REF: C42.1, U5.6 (REF_SENSE), U5.7 (REF)
/RESET: C28.1, IC1.F3 (RESET_B), J1.10 (NRST), TP8.1 (1_1)
/SPI_MISO: IC1.C4 (P1_2), U2.7 (MISO)
/SPI_MOSI: IC1.C6 (P1_0), U2.4 (MOSI)
/SPI_SCK: IC1.C5 (P1_1), U2.12 (SCLK)
/SPI_nCS: IC1.B4 (P1_3), U2.5 (~CS)
/UART_RX: IC1.A1 (P1_8), J2.23, J2.24
/UART_TX: IC1.B1 (P1_9), J2.21, J2.22
/USB_D+: IC1.T14 (USB0_DM), J1.3 (DEVICE-D+)
/USB_D-: IC1.T15 (USB0_DP), J1.4 (DEVICE-D-)
/VBUS_VSNS: IC1.U2 (ANA_6), R7.2, R8.1
/VREG: C38.1, U5.8 (VREG)
GND: C1.2, C2.2, C5.2, C6.2, C7.2, C8.2, C9.1, C10.2, C11.2, C12.1, C13.2, C14.1, C15.1, C16.2, C17.2, C18.1, C19.2, C20.1, C21.2, C22.2, C23.2, C24.2, C25.2, C26.2, C27.2, C28.2, C29.2, C30.2, C31.2, C32.2, C33.2, C34.2, C35.2, C36.2, C37.2, C38.2, C39.2, C40.2, C41.2, C42.2, C43.1, C44.1, C48.2, C55.2, D1.1 (K), D2.1 (K), IC1.D6 (VSS_1), IC1.D9 (VSS_2), IC1.D12 (VSS_3), IC1.E5 (VSS_4), IC1.E13 (VSS_5), IC1.G2 (VSS_6), IC1.H5 (VSS_7), IC1.H9 (VSS_8), IC1.H13 (VSS_9), IC1.J4 (VSS_10), IC1.J8 (VSS_11), IC1.J10 (VSS_12), IC1.J14 (VSS_13), IC1.K9 (VSS_14), IC1.N13 (VSS_15), IC1.P6 (VSS_P4_1), IC1.P7 (VSS_P4_2), IC1.P9 (VSS_P4_3), IC1.P12 (VSS_16), IC1.P14 (VSS_17), IC1.P16 (VSS_DCDC), IC1.R6 (VREFL), IC1.T16 (VSS_18), J1.5 (GND), J1.14 (GND), J1.15 (PAD), J1.16 (PAD), NT1.2, R3.2, R4.2, R5.2, R8.2, U1.2 (GND), U2.8 (GND), U2.10 (TEST), U2.15 (SSCK), U2.17 (PAD), U3.11 (EP/GND), U4.9 (GND), U4.10 (GND), U5.11 (GND), U6.3 (GND), Y1.2 (G), Y1.4 (G); also elsewhere on the board
unnamed: C45.2, R14.1
unnamed: C46.2, R15.1
unnamed: C47.2, R16.1
unnamed: D1.2 (A), R1.2
unnamed: D2.2 (A), R9.2
unnamed: FB1.1, R6.2
unnamed: FB5.1, TH1.1
unnamed: FB6.1, R18.2
unnamed: IC1.P17 (DCDC_LX), L1.2
unnamed: IC1.U14 (USB1_VBUS), R5.1
unnamed: C19.1, C21.1, C23.1, IC1.K10 (VDD_CORE_1), IC1.L11 (VDD_CORE_2), L1.1
unnamed: C17.1, IC1.N14 (VDD_SYS)
unnamed: C33.1, IC1.F1 (P1_30), Y1.3
unnamed: C32.1, IC1.F2 (P1_31), Y1.1
unnamed: IC1.B17 (P3_0), R9.1
unnamed: R4.1, U3.7 (FB/VSET)
unnamed: R3.1, U3.4 (MODE/S-CONF)
unnamed: C11.1, U3.5 (SS/TR)
unnamed: R17.2, R19.1, U6.2 (OUT)
PGND: C3.2, C4.2, C49.2, C50.2, C51.2, C52.2, C53.2, C54.2, C56.2, C57.2, J2.9, J2.10, J2.11, J2.12, J2.13, J2.14, J2.15, J2.16, NT1.1, R14.2, R15.2, R16.2, TH1.2, TP1.1 (1_1), TP2.1 (1_1); also elsewhere on the board
VBUS: C3.1, C4.1, C5.1, C6.1, C8.1, C49.1, C50.1, C51.1, C52.1, C53.1, C54.1, C56.1, C57.1, J2.1, J2.2, J2.3, J2.4, J2.5, J2.6, J2.7, J2.8, R7.1, U3.1 (VIN), U3.2 (VIN), U3.3 (EN); also elsewhere on the board

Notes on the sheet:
MCXN947VDFT (BGA Package)
4.7mW
8uF/ea @ 3.3V
GRT188C81C106ME13 0603 -55-105C AEC-Q200
Bypass
-15dB @ 100kHz -55dB @ 1MHz
populate in case something is throwing garbage onto the 3v3a in the GND snorkel
place at PGND->DGND plane cross
3mW
Bulk caps
GRT188C80J226ME13D 0603 -55-105C AEC-Q200
VBAT->5V SMPS
500mA max
Port 1 (CAN,SPI,UART,THERMS,XTAL)
CAN XCVR
tau=40ns for S&H time
EN ok to connect to VCC
2.4ms soft start
5mV output ripple
Port 4 (ADC/Analog)
10mV ripple
Port 3 (Unused GPIOs)
ADCS CARD MEZZ
1.68k thevenin
Internal PD
This goes somewhere kinda further from inverter
if you need more than four reaction wheels on a single CAN bus, please double check your universe's number of cardinal directions and ensure you did not accidentally include a temporal dimension.
Mag encoder
Star at breakaway to inverter
EMI filtering
ISPMODE_N
Power LED (Remove B4 Flight)
100kHz-4MHz Fsw (PWM/PFM)
GRM32EC81C476ME15L
Damped verified OK
4uF/ea @ 5V
Phases
New OreSat FFC Debug
Heartbeat LED (Remove B4 Flight)
fixed 3V3

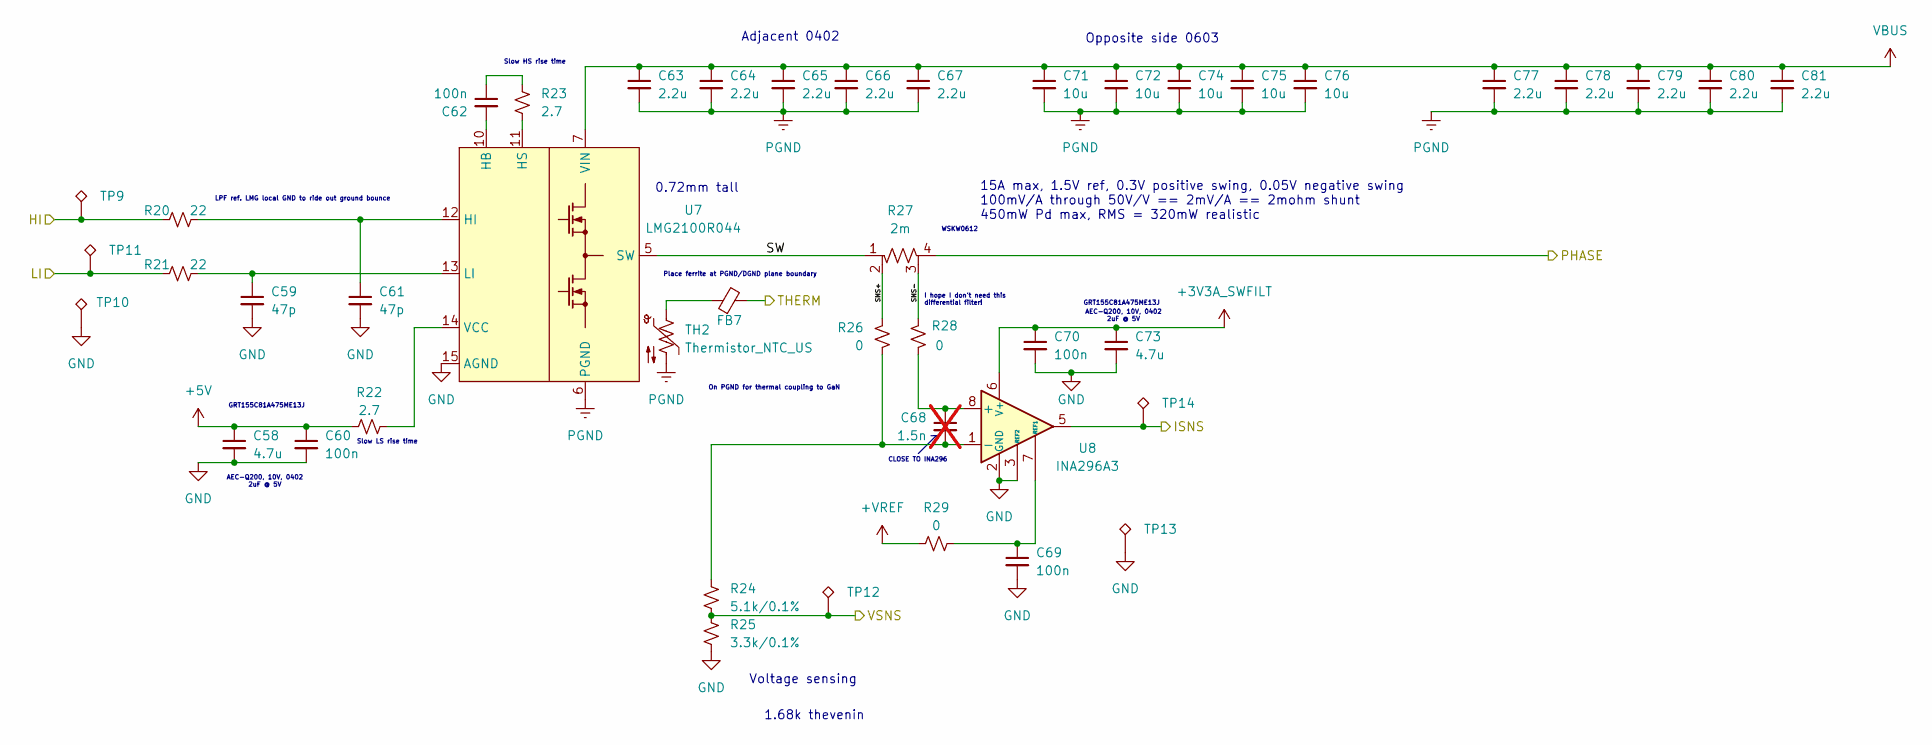
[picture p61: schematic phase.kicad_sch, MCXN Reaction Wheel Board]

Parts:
C58, C73: 4.7u; C_0402_1005Metric; MPN GRT155C81A475ME13J
C59, C61: 47p; C_0402_1005Metric; MPN GCM1555C1H470JA16D
C60, C62, C69, C70: 100n; C_0402_1005Metric; MPN GRT155R71E104KE01J
C63, C64, C65, C66, C67, C77, C78, C79, C80, C81: 2.2u; C_0402_1005Metric; MPN GRT155C81C225ME13D
C68: 1.5n; C_0402_1005Metric; MPN GCM155R71H152KA37D; not fitted
C71, C72, C74, C75, C76: 10u; C_0603_1608Metric; MPN GRT188C81C106ME13D
FB7: BLM15PX601SZ1; L_0402_1005Metric; MPN BLM15PX601SZ1D
R20, R21: 22; R_0402_1005Metric; MPN AC0402FR-0722RL
R22, R23: 2.7; R_0402_1005Metric; MPN AC0402FR-072R7L
R24: 5.1k/0.1%; R_0402_1005Metric; MPN RP0402BRD075K1L
R25: 3.3k/0.1%; R_0402_1005Metric; MPN RP0402BRD073K3L
R26, R28, R29: 0; R_0402_1005Metric; MPN AC0402FR-070RL
R27: 2m; R_Shunt_Vishay_WSKW0612; MPN WSKW06122L000FEA
TH2: Thermistor_NTC_US; R_0402_1005Metric; MPN NCU15XH103F6SRC
TP9, TP10, TP11, TP12, TP13, TP14: TestPoint_Alt; TestPoint_Pad_1.0x1.0mm_NoSilk
U7: LMG2100R044; TI_torment_nexus; MPN LMG2100R044RARR
U8: INA296A3; SOT-23-8; MPN INA296A3QDDFRQ1

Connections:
+3V3A_SWFILT: C70.1, C73.1, U8.6 (V+); also elsewhere on the board
+5V: C58.1, C60.1, R22.1; also elsewhere on the board
+VREF: R29.1; also elsewhere on the board
/PHA_HI: R20.2, TP9.1 (1_1); also elsewhere on the board
/PHA_ISNS: TP14.1 (1_1), U8.5; also elsewhere on the board
/PHA_LI: R21.1, TP11.1 (1_1); also elsewhere on the board
/PHA_SW: R27.4; also elsewhere on the board
/PHA_THERM: FB7.2; also elsewhere on the board
/PHA_VSNS: R24.2, R25.1, TP12.1 (1_1); also elsewhere on the board
/Phase A/SNS+: R26.1, R27.2
/Phase A/SNS-: R27.3, R28.2
/Phase A/SW: R27.1, U7.5 (SW)
GND: C58.2, C59.2, C60.2, C61.2, C69.2, C70.2, C73.2, R25.2, TP10.1 (1_1), TP13.1 (1_1), U7.15 (AGND), U8.2 (GND), U8.3 (REF2), U8.4 (GND); also elsewhere on the board
unnamed: C62.1, R23.1
unnamed: FB7.1, TH2.1
unnamed: C62.2, U7.10 (HB)
unnamed: C61.1, R20.1, U7.12 (HI)
unnamed: R23.2, U7.11 (HS)
unnamed: C59.1, R21.2, U7.13 (LI)
unnamed: R22.2, U7.14 (VCC)
unnamed: C68.1, R28.1, U8.8 (+)
unnamed: C68.2, R24.1, R26.2, U8.1 (-)
unnamed: C69.1, R29.2, U8.7 (REF1)
PGND: C63.2, C64.2, C65.2, C66.2, C67.2, C71.2, C72.2, C74.2, C75.2, C76.2, C77.2, C78.2, C79.2, C80.2, C81.2, TH2.2, U7.6 (PGND), U7.17 (PGND); also elsewhere on the board
VBUS: C63.1, C64.1, C65.1, C66.1, C67.1, C71.1, C72.1, C74.1, C75.1, C76.1, C77.1, C78.1, C79.1, C80.1, C81.1, U7.7 (VIN); also elsewhere on the board

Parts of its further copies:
C82, C97, C106, C121: 4.7u; C_0402_1005Metric; MPN GRT155C81A475ME13J
C83, C85, C107, C109: 47p; C_0402_1005Metric; MPN GCM1555C1H470JA16D
C84, C86, C93, C94, C108, C110, C117, C118: 100n; C_0402_1005Metric; MPN GRT155R71E104KE01J
C87, C88, C89, C90, C91, C101, C102, C103, C104, C105, C111, C112, C113, C114, C115, C125, C126, C127, C128, C129: 2.2u; C_0402_1005Metric; MPN GRT155C81C225ME13D
C92, C116: 1.5n; C_0402_1005Metric; MPN GCM155R71H152KA37D; not fitted
C95, C96, C98, C99, C100, C119, C120, C122, C123, C124: 10u; C_0603_1608Metric; MPN GRT188C81C106ME13D
FB8, FB9: BLM15PX601SZ1; L_0402_1005Metric; MPN BLM15PX601SZ1D
R30, R31, R40, R41: 22; R_0402_1005Metric; MPN AC0402FR-0722RL
R32, R33, R42, R43: 2.7; R_0402_1005Metric; MPN AC0402FR-072R7L
R34, R44: 5.1k/0.1%; R_0402_1005Metric; MPN RP0402BRD075K1L
R35, R45: 3.3k/0.1%; R_0402_1005Metric; MPN RP0402BRD073K3L
R36, R38, R39, R46, R48, R49: 0; R_0402_1005Metric; MPN AC0402FR-070RL
R37, R47: 2m; R_Shunt_Vishay_WSKW0612; MPN WSKW06122L000FEA
TH3, TH4: Thermistor_NTC_US; R_0402_1005Metric; MPN NCU15XH103F6SRC
TP15, TP16, TP17, TP18, TP19, TP20, TP21, TP22, TP23, TP24, TP25, TP26: TestPoint_Alt; TestPoint_Pad_1.0x1.0mm_NoSilk
U9, U11: LMG2100R044; TI_torment_nexus; MPN LMG2100R044RARR
U10, U12: INA296A3; SOT-23-8; MPN INA296A3QDDFRQ1

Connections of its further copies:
+3V3A_SWFILT: C94.1, C97.1, C118.1, C121.1, U10.6 (V+), U12.6 (V+); also elsewhere on the board
+5V: C82.1, C84.1, C106.1, C108.1, R32.1, R42.1; also elsewhere on the board
+VREF: R39.1, R49.1; also elsewhere on the board
/PHB_HI: R30.2, TP15.1 (1_1); also elsewhere on the board
/PHB_ISNS: TP20.1 (1_1), U10.5; also elsewhere on the board
/PHB_LI: R31.1, TP17.1 (1_1); also elsewhere on the board
/PHB_SW: R37.4; also elsewhere on the board
/PHB_THERM: FB8.2; also elsewhere on the board
/PHB_VSNS: R34.2, R35.1, TP18.1 (1_1); also elsewhere on the board
/PHC_HI: R40.2, TP21.1 (1_1); also elsewhere on the board
/PHC_ISNS: TP26.1 (1_1), U12.5; also elsewhere on the board
/PHC_LI: R41.1, TP23.1 (1_1); also elsewhere on the board
/PHC_SW: R47.4; also elsewhere on the board
/PHC_THERM: FB9.2; also elsewhere on the board
/PHC_VSNS: R44.2, R45.1, TP24.1 (1_1); also elsewhere on the board
/Phase B/SNS+: R36.1, R37.2
/Phase B/SNS-: R37.3, R38.2
/Phase B/SW: R37.1, U9.5 (SW)
/Phase C/SNS+: R46.1, R47.2
/Phase C/SNS-: R47.3, R48.2
/Phase C/SW: R47.1, U11.5 (SW)
GND: C82.2, C83.2, C84.2, C85.2, C93.2, C94.2, C97.2, C106.2, C107.2, C108.2, C109.2, C117.2, C118.2, C121.2, R35.2, R45.2, TP16.1 (1_1), TP19.1 (1_1), TP22.1 (1_1), TP25.1 (1_1), U9.15 (AGND), U10.2 (GND), U10.3 (REF2), U10.4 (GND), U11.15 (AGND), U12.2 (GND), U12.3 (REF2), U12.4 (GND); also elsewhere on the board
unnamed: C86.1, R33.1
unnamed: C110.1, R43.1
unnamed: FB8.1, TH3.1
unnamed: FB9.1, TH4.1
unnamed: C86.2, U9.10 (HB)
unnamed: C85.1, R30.1, U9.12 (HI)
unnamed: R33.2, U9.11 (HS)
unnamed: C83.1, R31.2, U9.13 (LI)
unnamed: R32.2, U9.14 (VCC)
unnamed: C92.1, R38.1, U10.8 (+)
unnamed: C92.2, R34.1, R36.2, U10.1 (-)
unnamed: C93.1, R39.2, U10.7 (REF1)
unnamed: C110.2, U11.10 (HB)
unnamed: C109.1, R40.1, U11.12 (HI)
unnamed: R43.2, U11.11 (HS)
unnamed: C107.1, R41.2, U11.13 (LI)
unnamed: R42.2, U11.14 (VCC)
unnamed: C116.1, R48.1, U12.8 (+)
unnamed: C116.2, R44.1, R46.2, U12.1 (-)
unnamed: C117.1, R49.2, U12.7 (REF1)
PGND: C87.2, C88.2, C89.2, C90.2, C91.2, C95.2, C96.2, C98.2, C99.2, C100.2, C101.2, C102.2, C103.2, C104.2, C105.2, C111.2, C112.2, C113.2, C114.2, C115.2, C119.2, C120.2, C122.2, C123.2, C124.2, C125.2, C126.2, C127.2, C128.2, C129.2, TH3.2, TH4.2, U9.6 (PGND), U9.17 (PGND), U11.6 (PGND), U11.17 (PGND); also elsewhere on the board
VBUS: C87.1, C88.1, C89.1, C90.1, C91.1, C95.1, C96.1, C98.1, C99.1, C100.1, C101.1, C102.1, C103.1, C104.1, C105.1, C111.1, C112.1, C113.1, C114.1, C115.1, C119.1, C120.1, C122.1, C123.1, C124.1, C125.1, C126.1, C127.1, C128.1, C129.1, U9.7 (VIN), U11.7 (VIN); also elsewhere on the board

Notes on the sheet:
0.72mm tall
I hope I don't need this differential filter!
On PGND for thermal coupling to GaN
1.68k thevenin
Opposite side 0603
Adjacent 0402
WSKW0612
GRT155C81A475ME13J
Slow HS rise time
Voltage sensing
AEC-Q200, 10V, 0402 2uF @ 5V
Place ferrite at PGND/DGND plane boundary
Slow LS rise time
LPF ref. LMG local GND to ride out ground bounce
CLOSE TO INA296
15A max, 1.5V ref, 0.3V positive swing, 0.05V negative swing 100mV/A through 50V/V == 2mV/A == 2mohm shunt 450mW Pd max, RMS = 320mW realistic

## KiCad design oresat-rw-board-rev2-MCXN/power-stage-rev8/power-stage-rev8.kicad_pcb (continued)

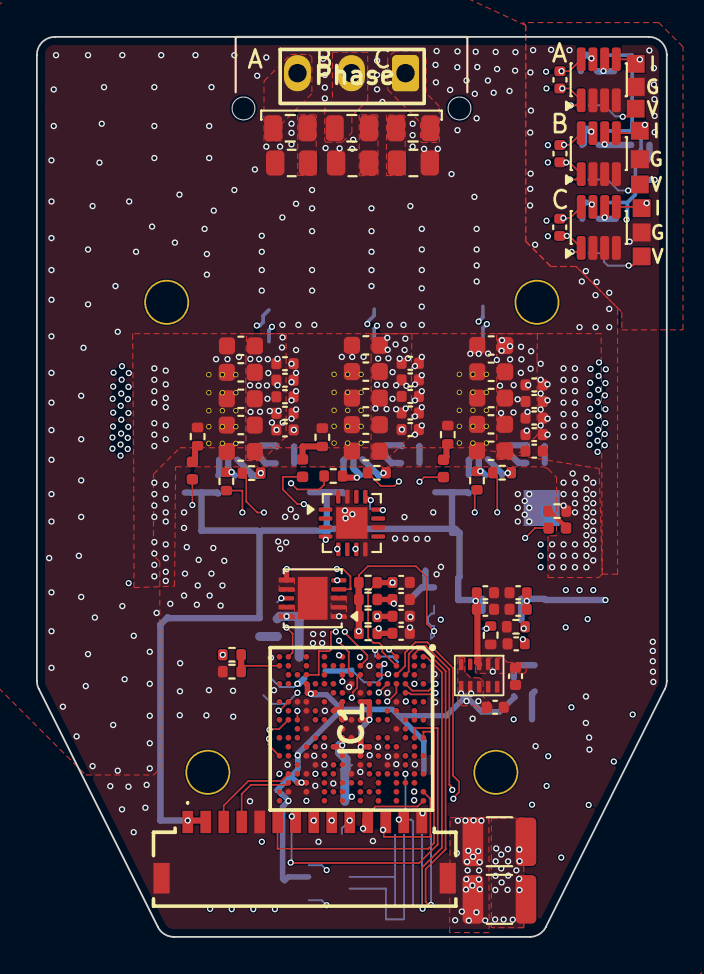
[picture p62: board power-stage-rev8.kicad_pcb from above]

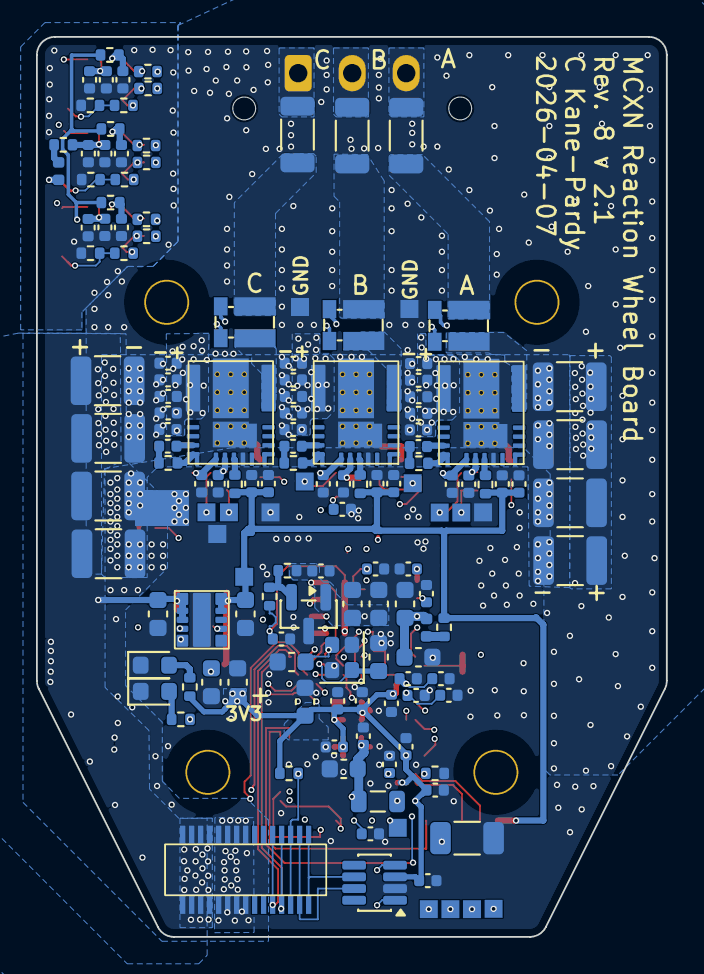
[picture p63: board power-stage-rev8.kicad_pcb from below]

Board: 6 copper layers, 35.0 x 50.0 mm, 239 parts (146 on the bottom side), 112 nets.

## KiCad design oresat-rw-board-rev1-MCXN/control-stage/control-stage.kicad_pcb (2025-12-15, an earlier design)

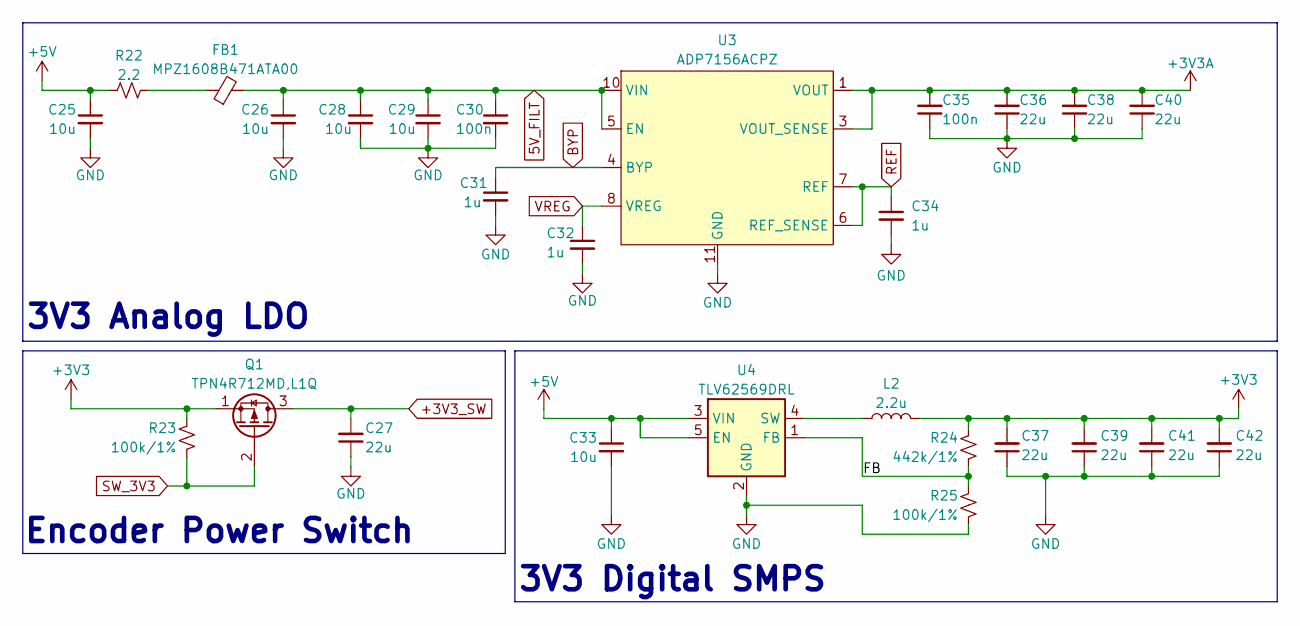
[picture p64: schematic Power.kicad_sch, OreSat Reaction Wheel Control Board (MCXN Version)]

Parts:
C25, C26, C28, C29, C33: 10u; C_0603_1608Metric; Mfg P/N GRM188R61A106KE69J
C27, C36, C37, C38, C39, C40, C41, C42: 22u; C_0603_1608Metric; Mfg P/N GRM188R61A226ME15D
C30, C35: 100n; C_0402_1005Metric; Mfg P/N GRM155R61A104KA01J
C31, C32, C34: 1u; C_0402_1005Metric; Mfg P/N GRT155R61A105KE01D
FB1: MPZ1608B471ATA00; L_0603_1608Metric; Mfg P/N MPZ1608B471ATA00
L2: 2.2u; L_1008_2520Metric; Mfg P/N DFE252012PD-2R2M=P2
Q1: TPN4R712MD,L1Q; TSON-Advance; Mfg P/N TPN4R712MD,L1Q
R22: 2.2; R_0603_1608Metric; Mfg P/N AF0603FR-072R2L
R23, R25: 100k/1%; R_0402_1005Metric; Mfg P/N AC0402FR-13100KL
R24: 442k/1%; R_0402_1005Metric; Mfg P/N RMCF0402FT442K
U3: ADP7156ACPZ; DFN-10-1EP_3x3mm_P0.5mm_EP1.65x2.38mm; Mfg P/N ADP7156ACPZ-3.3-R7
U4: TLV62569DRL; SOT-563; Mfg P/N TLV62569ADRLR

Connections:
5V_FILT: C26.1, C28.1, C29.1, C30.1, FB1.2, U3.5 (EN), U3.9 (VIN), U3.10 (VIN)
+3V3: C37.2, C39.2, C41.2, C42.2, L2.2, Q1.1 (S), R23.2, R24.2; also elsewhere on the board
+3V3A: C35.2, C36.2, C38.2, C40.2, U3.1 (VOUT), U3.2 (VOUT), U3.3 (VOUT_SENSE); also elsewhere on the board
+3V3_SW: C27.2, Q1.3 (D); also elsewhere on the board
+5V: C25.1, C33.1, R22.1, U4.3 (VIN), U4.5 (EN); also elsewhere on the board
/Power Architecture/FB: R24.1, R25.2, U4.1 (FB)
BYP: C31.1, U3.4 (BYP)
GND: C25.2, C26.2, C27.1, C28.2, C29.2, C30.2, C31.2, C32.2, C33.2, C34.2, C35.1, C36.1, C37.1, C38.1, C39.1, C40.1, C41.1, C42.1, R25.1, U3.11 (GND), U4.2 (GND); also elsewhere on the board
unnamed: FB1.1, R22.2
unnamed: L2.1, U4.4 (SW)
REF: C34.1, U3.6 (REF_SENSE), U3.7 (REF)
SW_3V3: Q1.2 (G), R23.1; also elsewhere on the board
VREG: C32.1, U3.8 (VREG)

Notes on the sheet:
3V3 Digital SMPS
3V3 Analog LDO
Encoder Power Switch


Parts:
C19, C20: 47u; C_1210_3225Metric; Mfg P/N GRM32ER71A476KE15L
C21: 100n; C_0402_1005Metric; Mfg P/N GRM155R61A104KA01J
C22: 10p; C_0402_1005Metric; Mfg P/N GRM1555C1H100JA01D
H1: Board_Def; top-board-def-rev7.1
J1: Power Mezz; 10132798-021100LF; Mfg P/N 10132798-021100LF
J2: Analog Mezz; 10132798-021100LF; Mfg P/N 10132798-021100LF
J3: Phase Mezz; 10132798-021100LF; Mfg P/N 10132798-021100LF
J4: ADCS Mezz; 0555600307; Mfg P/N 555600307
NT1: NetTie; NetTie_ADCS
R8, R9, R10, R11, R12, R13, R14, R15: THJP1206ABT1; R_1206_3216Metric; Mfg P/N THJP1206ABT1
R16: 5.1k/0.1%; R_0402_1005Metric; Mfg P/N RP0402BRD075K1L
R17: 3.3k/0.1%; R_0402_1005Metric; Mfg P/N RP0402BRD073K3L
U2: TCAN330; SOT-23-8-Fixed; Mfg P/N TCAN330DCNR

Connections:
+3V3: C21.1, U2.3 (VCC); also elsewhere on the board
+3V3A: J2.1, J2.20; also elsewhere on the board
+3V3_SW: J3.10, J3.11; also elsewhere on the board
+5V: C20.1, J1.9, J1.10, J1.11, J1.12, J4.17, J4.18, J4.19, J4.20; also elsewhere on the board
BOOT0: J4.25, J4.26; also elsewhere on the board
CAN_N: J4.29, J4.30, U2.6 (CANL)
CAN_P: J4.27, J4.28, U2.7 (CANH)
CAN_RX: U2.4 (RXD); also elsewhere on the board
CAN_TX: U2.1 (TXD); also elsewhere on the board
Chassis: H1.1, R8.1, R9.1, R10.1, R11.1, R12.1, R13.1, R14.1, R15.1
ENC_A: J3.9; also elsewhere on the board
ENC_B: J3.12; also elsewhere on the board
GND: C20.2, C21.2, C22.2, J1.7, J1.8, J1.13, J1.14, J1.MP (MountPin), J2.2, J2.4, J2.6, J2.8, J2.10, J2.11, J2.13, J2.15, J2.17, J2.19, J2.MP (MountPin), J3.1, J3.5, J3.8, J3.13, J3.16, J3.20, J3.MP (MountPin), NT1.2, R8.2, R9.2, R10.2, R11.2, R12.2, R13.2, R14.2, R15.2, R17.1, U2.2 (GND), U2.8 (S); also elsewhere on the board
PGND: C19.2, J1.4, J1.5, J1.6, J1.15, J1.16, J1.17, J4.9, J4.10, J4.11, J4.12, J4.13, J4.14, J4.15, J4.16, NT1.1
PHA_H: J3.2; also elsewhere on the board
PHA_ISNS: J2.5, J2.16; also elsewhere on the board
PHA_L: J3.19; also elsewhere on the board
PHB_H: J3.3; also elsewhere on the board
PHB_ISNS: J2.7, J2.14; also elsewhere on the board
PHB_L: J3.18; also elsewhere on the board
PHC_H: J3.4; also elsewhere on the board
PHC_ISNS: J2.9, J2.12; also elsewhere on the board
PHC_L: J3.17; also elsewhere on the board
SPI_MISO: J3.7; also elsewhere on the board
SPI_MOSI: J3.6; also elsewhere on the board
SPI_SCK: J3.15; also elsewhere on the board
SPI_nCS: J3.14; also elsewhere on the board
THERM_A: J2.18; also elsewhere on the board
THERM_B: J2.3; also elsewhere on the board
UART_RX: J4.23, J4.24; also elsewhere on the board
UART_TX: J4.21, J4.22; also elsewhere on the board
VBUS: C19.1, J1.1, J1.2, J1.3, J1.18, J1.19, J1.20, J4.1, J4.2, J4.3, J4.4, J4.5, J4.6, J4.7, J4.8, R16.1
VBUS_VSNS: C22.1, R16.2, R17.2; also elsewhere on the board

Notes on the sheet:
Power
Mezzanine Connector to ADCS Card
Thermal Jumpers
Phase/SPI
Analog
Mezzanine Connectors to Motor Board


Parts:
C1, C15: 10u; C_0603_1608Metric; Mfg P/N GRM188R61A106KE69J
C2, C8, C10: 4.7u; C_0603_1608Metric; Mfg P/N GRM185R61A475KE11D
C3, C4, C6, C7, C9, C11, C13, C14, C16, C17, C18: 100n; C_0402_1005Metric; Mfg P/N GRM155R61A104KA01J
C5: 1u; C_0402_1005Metric; Mfg P/N GRT155R61A105KE01D
C12: 6.8u; C_1206_3216Metric; Mfg P/N CGA5L1X7R1C685M160AC
C43, C44: 4.7p; 0603-C-NOSILK; MPN GRM1885C1H4R7WA01D
D1, D2: Green; LED_0603_1608Metric; Mfg P/N 150060VS55040
L1: 1.5u; L_0805_2012Metric; MPN SRP2012TMA-1R5M
R1: 17.8k/1%; R_0603_1608Metric; Mfg P/N ERJ-UP3F1782V
R2: 33k/1%; R_0603_1608Metric; Mfg P/N ERJ-UP3F3302V
R3, R5: 10k/NTC; R_0402_1005Metric; Mfg P/N NCU15XH103F6SRC
R4, R6, R7: 10k; R_0402_1005Metric; Mfg P/N AC0402DR-0710KL
R26, R27: 100; R_0402_1005Metric; Mfg P/N SR0402FR-7T100RL
SW1: BOOT0; SW_Push_SPST_NO_Alps_SKRK; Mfg P/N SKRKAGE020
U1: MCXN947VKLT; MCXN947KVLT-QFP50P1600X1600X160-101N; MPN MCXN947VKLT
Y1: 24 MHz; Crystal_SMD_2016-4Pin_2.0x1.6mm; MPN 830108212309

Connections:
+3V3: C1.2, C2.2, C4.2, C6.2, C7.2, C9.2, C11.2, C14.2, C16.2, R7.1, R27.1, U1.13 (VDD_LDO_CORE/VDD/VDD_P2), U1.34 (VDD_P4), U1.47 (VDD_BAT), U1.54 (VDD_DCDC/VDD_LDO_SYS), U1.59 (VDD_P3), U1.66 (VDD_P3), U1.73 (VDD_P3), U1.83 (VDD), U1.96 (VDD); also elsewhere on the board
+3V3A: C10.1, C13.1, C17.1, R3.1, R5.1, U1.30 (VDD_ANA), U1.31 (VREFH); also elsewhere on the board
BOOT0: R7.2, SW1.2, U1.82 (ISPMODE_N); also elsewhere on the board
CAN_RX: U1.4 (CAN0_RXD); also elsewhere on the board
CAN_TX: U1.3 (CAN0_TXD); also elsewhere on the board
DEBUG0: U1.79 (P0_3); also elsewhere on the board
DEBUG1: U1.80 (P0_4); also elsewhere on the board
DEBUG2: U1.81 (P0_5); also elsewhere on the board
DEBUG3: U1.74 (P3_1); also elsewhere on the board
DEBUG_RX: U1.84 (P0_16); also elsewhere on the board
DEBUG_SWCLK: U1.77 (TCLK/SWCLK); also elsewhere on the board
DEBUG_SWDIO: U1.76 (TMS/SWDIO); also elsewhere on the board
DEBUG_SWO: U1.78 (TDO/SWO); also elsewhere on the board
DEBUG_TX: U1.85 (P0_17); also elsewhere on the board
ENC_A: U1.20 (TRIG_IN4); also elsewhere on the board
ENC_B: U1.21 (TRIG_IN5); also elsewhere on the board
GND: C1.1, C2.1, C3.1, C4.1, C5.2, C6.1, C7.1, C8.2, C9.1, C10.2, C11.1, C12.2, C13.2, C14.1, C15.2, C16.1, C17.2, C18.2, C43.2, C44.2, D1.1 (K), D2.1 (K), R2.1, R4.2, R6.2, SW1.1, U1.32 (VREFL), U1.33 (VSS_P4), U1.52 (VSS_DCDC), U1.101 (EP), Y1.2, Y1.4; also elsewhere on the board
unnamed: C12.1, C15.1, C18.1, L1.1, U1.12 (VDD_CORE), U1.58 (VDD_CORE)
unnamed: D1.2 (A), R27.2
unnamed: D2.2 (A), R26.2
unnamed: L1.2, U1.53 (DCDC_LX)
unnamed: C8.1, U1.55 (VDD_SYS)
unnamed: C3.2, C5.1, R1.1, R2.2, U1.44 (VDD_USB)
unnamed: C44.1, U1.10 (XTAL48M), Y1.3
unnamed: C43.1, U1.11 (EXTAL48M), Y1.1
unnamed: R26.1, U1.69 (P3_9)
PHA_H: U1.14 (P2_0); also elsewhere on the board
PHA_ISNS: U1.22 (ADC0_A0); also elsewhere on the board
PHA_L: U1.15 (P2_1); also elsewhere on the board
PHB_H: U1.16 (P2_2); also elsewhere on the board
PHB_ISNS: U1.26 (ADC1_A0); also elsewhere on the board
PHB_L: U1.17 (P2_3); also elsewhere on the board
PHC_H: U1.18 (P2_4); also elsewhere on the board
PHC_ISNS: U1.28 (DAC2_OUT/ADC0_A3/ADC1_A3); also elsewhere on the board
PHC_L: U1.19 (P2_5); also elsewhere on the board
RESET: U1.9 (RESET_B); also elsewhere on the board
SCOPE0: U1.27 (ADC1_B0); also elsewhere on the board
SCOPE1: U1.29 (VREFI/VREFO/ADC0_A7/ADC1_A7); also elsewhere on the board
SCOPE2: U1.35 (OPAMP0_INP0/ADC0_A5/ADC1_A5); also elsewhere on the board
SPI_MISO: U1.94 (SPI_SDI); also elsewhere on the board
SPI_MOSI: U1.92 (SPI_SDO); also elsewhere on the board
SPI_SCK: U1.93 (SPI_SCK); also elsewhere on the board
SPI_nCS: U1.7 (P1_14); also elsewhere on the board
SW_3V3: U1.75 (P3_0); also elsewhere on the board
THERM_A: R5.2, R6.1, U1.25 (DAC1_OUT/ADC0_B4/ADC1_B4/CMP0_IN5N/CMP1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); also elsewhere on the board
THERM_B: R3.2, R4.1, U1.24 (DAC0_OUT/ADC0_A4/ADC1_A4/CMP0_IN4N/CMP1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); also elsewhere on the board
UART_RX: U1.1 (ISP-UART_RXD); also elsewhere on the board
UART_TX: U1.2 (ISP-UART_TXD); also elsewhere on the board
USB0_DM: U1.45 (USB0_DM); also elsewhere on the board
USB0_DP: U1.46 (USB0_DP); also elsewhere on the board
VBUS_VSNS: U1.23 (ADC0_B0); also elsewhere on the board
V_USB: R1.2; also elsewhere on the board


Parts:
C23, C24: 100n; C_0402_1005Metric; Mfg P/N GRM155R61A104KA01J
J5: Debug; J-TE_2-1734592-0; Mfg P/N 2-1734592-0
J6: USB-C; USB_C_Receptacle_Palconn_UTC16-G
J7: PROBE; PinHeader_2x05_P1.27mm_Horizontal; Mfg P/N FTSH-105-02-L-DV-A
R18: 1M; R_0805_2012Metric; Mfg P/N RCS08051M00FKEA
R19, R20: 5.11k; C_0603_1608Metric; Mfg P/N ERJ-UP3F5111V
R21: 10k; R_0402_1005Metric; Mfg P/N AC0402DR-0710KL
SW2: RESET; SW_Push_SPST_NO_Alps_SKRK; Mfg P/N SKRKAGE020
TP1, TP2, TP3, TP4, TP5, TP6: TestPoint_Alt; TestPoint_THTPad_1.0x1.0mm_Drill0.5mm

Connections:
+3V3: J5.11 (VTARGET), R21.2, TP1.1; also elsewhere on the board
+5V: J5.1 (VBUSP), J5.2 (VBUSP); also elsewhere on the board
BOOT0: J5.17 (DEBUG-0); also elsewhere on the board
DEBUG0: J7.1; also elsewhere on the board
DEBUG1: J7.3; also elsewhere on the board
DEBUG2: J7.5; also elsewhere on the board
DEBUG3: J7.7; also elsewhere on the board
DEBUG_RX: J5.12 (CARD-RX), J7.4; also elsewhere on the board
DEBUG_SWCLK: J5.15 (SWCLK), TP3.1; also elsewhere on the board
DEBUG_SWDIO: J5.14 (SWDIO), TP4.1; also elsewhere on the board
DEBUG_SWO: J5.16 (SWO), TP5.1; also elsewhere on the board
DEBUG_TX: J5.13 (CARD-TX), J7.2; also elsewhere on the board
GND: C23.2, C24.2, J5.3 (GND), J5.6 (GND), J5.9 (GND), J5.PAD1 (PAD), J5.PAD2 (PAD), J6.A1 (GND), J6.A12 (GND), J6.B1 (GND), J6.B12 (GND), J7.9, R18.1, R19.1, R20.1, SW2.2, TP6.1; also elsewhere on the board
unnamed: J6.A5 (CC1), R20.2
unnamed: J6.B5 (CC2), R19.2
unnamed: C23.1, J6.S1 (SHIELD), R18.2
RESET: C24.1, J5.10 (NRST), R21.1, SW2.1, TP2.1; also elsewhere on the board
SCOPE0: J7.10; also elsewhere on the board
SCOPE1: J7.8; also elsewhere on the board
SCOPE2: J7.6; also elsewhere on the board
UART_RX: J5.19 (DEBUG-2); also elsewhere on the board
UART_TX: J5.18 (DEBUG-1); also elsewhere on the board
USB0_DM: J6.A6 (D+), J6.B6 (D+); also elsewhere on the board
USB0_DP: J6.A7 (D-), J6.B7 (D-); also elsewhere on the board
V_USB: J6.A4 (VBUS), J6.A9 (VBUS), J6.B4 (VBUS), J6.B9 (VBUS); also elsewhere on the board

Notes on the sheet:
USB-C
Fake Trace Connector
OreSat FFC Debug Connector
SWO Test points
RESET



Board: 6 copper layers, 40.0 x 36.5 mm, 99 parts (33 on the bottom side), 69 nets.

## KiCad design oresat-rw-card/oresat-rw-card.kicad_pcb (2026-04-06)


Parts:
C1: 10u 25V 0805; C_0805_2012Metric; MPN GRT21BC71E106KE13K
FID1, FID2, FID3, FID4, FID5, FID6: Fiducial; Fiducial_1mm_Mask2mm
J1: J-SAMTEC-TFM-120-01-L-D-RA; J-SAMTEC-TFM-120-X1-XXX-D-RA; MPN TFM-120-01-L-D-RA
J4, J5, J6, J101: 0555600307; J-MOLEX-555600307; MPN 0555600307
PCB1: ORESAT-CARD-V1.3-GENERIC-0RF; ORESAT-CARD-V1.3-0RF

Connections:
/C3-UART-RX: J1.38; also elsewhere on the board
/C3-UART-TX: J1.37; also elsewhere on the board
/CAN2_H: J1.17, J1.18, J4.14, J4.17, J5.14, J5.17, J6.14, J6.17, J101.14, J101.17
/CAN2_L: J1.19, J1.20, J4.15, J4.16, J5.15, J5.16, J6.15, J6.16, J101.15, J101.16
/OPD_PWR: J1.15, J1.16; also elsewhere on the board
/OPD_SCL: J1.13, J1.14; also elsewhere on the board
/OPD_SDA: J1.11, J1.12; also elsewhere on the board
/RW Power Domain Q1/BOOTCFG-Q1: J101.13, J101.18; also elsewhere on the board
/RW Power Domain Q1/RW-UART-RX-Q1: J101.12, J101.19; also elsewhere on the board
/RW Power Domain Q1/RW-UART-TX-Q1: J101.11, J101.20; also elsewhere on the board
/RW Power Domain Q1/VBUSP-Q1: J101.1, J101.2, J101.3, J101.4, J101.27, J101.28, J101.29, J101.30; also elsewhere on the board
/RW Power Domain Q2/BOOTCFG-Q2: J4.13, J4.18; also elsewhere on the board
/RW Power Domain Q2/RW-UART-RX-Q2: J4.12, J4.19; also elsewhere on the board
/RW Power Domain Q2/RW-UART-TX-Q2: J4.11, J4.20; also elsewhere on the board
/RW Power Domain Q2/VBUSP-Q2: J4.1, J4.2, J4.3, J4.4, J4.27, J4.28, J4.29, J4.30; also elsewhere on the board
/RW Power Domain Q3/BOOTCFG-Q3: J5.13, J5.18; also elsewhere on the board
/RW Power Domain Q3/RW-UART-RX-Q3: J5.12, J5.19; also elsewhere on the board
/RW Power Domain Q3/RW-UART-TX-Q3: J5.11, J5.20; also elsewhere on the board
/RW Power Domain Q3/VBUSP-Q3: J5.1, J5.2, J5.3, J5.4, J5.27, J5.28, J5.29, J5.30; also elsewhere on the board
/RW Power Domain Q4/BOOTCFG-Q4: J6.13, J6.18; also elsewhere on the board
/RW Power Domain Q4/RW-UART-RX-Q4: J6.12, J6.19; also elsewhere on the board
/RW Power Domain Q4/RW-UART-TX-Q4: J6.11, J6.20; also elsewhere on the board
/RW Power Domain Q4/VBUSP-Q4: J6.1, J6.2, J6.3, J6.4, J6.27, J6.28, J6.29, J6.30; also elsewhere on the board
GND: C1.2, J1.27, J1.28, J1.29, J1.30, J4.5, J4.6, J4.7, J4.8, J4.23, J4.24, J4.25, J4.26, J5.5, J5.6, J5.7, J5.8, J6.5, J6.6, J6.7, J6.8, J6.23, J6.24, J6.25, J6.26, J101.5, J101.6, J101.7, J101.8, J101.23, J101.24, J101.25, J101.26; also elsewhere on the board
unnamed: J5.23, J5.24, J5.25, J5.26
VBUS: C1.1, J1.23, J1.24, J1.25, J1.26; also elsewhere on the board

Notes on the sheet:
Q3(-X-Y)
Main OreSat Card Connector
DOUBLECHECK
Fiducials (on both sides of board)
Q4(+X-Y)
All caps are 0603 ceramic 10% X5R Vw>=25V unless marked
Q2(-X+Y)
Q1(+X+Y)
All resistors 0602 +/- 1% and AEC qualified unless marked
Mezzanine Plugs to Reaction Wheel Boards

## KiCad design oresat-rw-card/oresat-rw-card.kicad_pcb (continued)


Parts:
C2, C3, C6, C7: 1u; 0603-C-NOSILK; MPN GRT188R71E105KE13D
C4, C5, C8, C9: 100n; 0603-C-NOSILK; MPN C0603C104K5RACAUTO
C68: 10n; 0603-C-NOSILK; MPN C0603C103J5RACAUTO
C69: 470n; 0603-C-NOSILK; MPN C0603C474K3RACAUTO
D1: AMBER; LED_0603_1608Metric_Pad1.05x0.95mm_HandSolder; MPN 150060AS75000
D2: GREEN; LED_0603_1608Metric_Pad1.05x0.95mm_HandSolder; MPN 150060GS75000
Q1: DMP2240UDM-7; SOT-23-6; MPN DMP2240UDM-7
Q2, Q9: DMN3028LQ-7; SOT-23; MPN DMN3028LQ-7
Q3, Q4: DMPH2040UVTQ-7; TSOT-23-6; MPN DMPH2040UVTQ-7
R1: 10; 0603-C-NOSILK; MPN RMCF0603FT10R0
R2, R6, R7, R8, R12, R24, R25: 100; 0603-C-NOSILK; MPN RMCF0603FT100R
R3, R4, R5, R9, R10, R11, R13, R16, R17: 100; 0603-C-NOSILK; not fitted
R14, R15: 665k; 0603-C-NOSILK; MPN RMCF0603FT665K
R18, R23, R26, R28, R30, R32, R34, R36, R37, R38, R41, R49, R50: 10k; 0603-C-NOSILK; MPN RMCF0603FT10K0
R19, R20: 330k; 0603-C-NOSILK; MPN RMCF0603FT330K
R21, R22: 1M; 0603-C-NOSILK; MPN RMCF0603FT1M00
R27: 4.7k; 0603-C-NOSILK; MPN RMCF0603FT4K70
R29: 100k; 0603-C-NOSILK; MPN RMCF0603FT100K
R31: 15m; 1206-C; MPN CSNL1206FT15L0
R33: 0; 0603-C-NOSILK; MPN RMCF0603ZT0R00
R35: 0; 0603-C-NOSILK; not fitted
TP2, TP3, TP4, TP6, TP9, TP10, TP11, TP12, TP13, TP14, TP15, TP17: Test-Point; TestPoint-0.75mm-th
U1: MAX7310; QFN-16-1EP_4x4mm_P0.65mm_EP2.1x2.1mm; MPN MAX7310ATE
U2, U3: MIC842LYC5; SOT-353_SC-70-5; MPN MIC842LYC5-TR
U5: TS5A21366DCUR; VSSOP-8_2.3x2mm_P0.5mm; MPN TS5A21366DCUR
U18: MAX4211FETE; QFN-16-1EP_4x4mm_P0.65mm_EP2.1x2.1mm; MPN MAX4211FETE

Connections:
/C3-UART-RX: R24.1; also elsewhere on the board
/C3-UART-TX: R25.1; also elsewhere on the board
/OPD_PWR: R1.2; also elsewhere on the board
/OPD_SCL: R6.2; also elsewhere on the board
/OPD_SDA: R7.2; also elsewhere on the board
/RW Power Domain Q1/AD0: R12.1, R13.2, R16.1, R17.2, U1.1 (AD0)
/RW Power Domain Q1/AD1: R8.1, R9.2, R10.1, R11.2, U1.2 (AD1)
/RW Power Domain Q1/AD2: R2.1, R3.2, R4.1, R5.2, U1.3 (AD2)
/RW Power Domain Q1/BOOTCFG-Q1: U1.10 (IO5); also elsewhere on the board
/RW Power Domain Q1/CB-RESET: R32.2, TP13.1, U1.9 (IO4), U18.9 (CIN2-)
/RW Power Domain Q1/CB_CTRL: Q9.1 (G), R49.1, TP10.1, U18.3 (LE), U18.4 (COUT1), U18.6 (COUT2)
/RW Power Domain Q1/ON/~OFF: C5.1, C6.1, Q2.1 (G), R26.1, R27.2, TP9.1, U1.8 (IO3), U5.8 (Vcc), U18.1 (VCC), U18.2 (IN)
/RW Power Domain Q1/PEN-SCL-FILT: Q1.4 (D), R2.2, R8.2, R12.2, R19.2, TP3.1, U1.15 (SCL)
/RW Power Domain Q1/PEN-SDA-FILT: Q1.6 (D), R4.2, R10.2, R16.2, R20.2, TP4.1, U1.16 (SDA)
/RW Power Domain Q1/RW-UART-RX-Q1: U5.6 (COM2); also elsewhere on the board
/RW Power Domain Q1/RW-UART-TX-Q1: U5.2 (COM1); also elsewhere on the board
/RW Power Domain Q1/UART_EN: R23.2, U1.12 (IO7), U5.3 (IN2), U5.7 (IN1)
/RW Power Domain Q1/VBUSP-Q1: C7.1, C69.1, Q4.1 (D), Q4.2 (D), Q4.5 (D), Q4.6 (D), R41.2, TP17.1; also elsewhere on the board
/RW Power Domain Q1/~FAULT: Q9.3 (D), R38.1, TP15.1, U1.7 (IO2)
GND: C2.2, C3.2, C4.2, C5.2, C6.2, C8.2, C9.2, D1.1 (K), D2.1 (K), Q2.2 (S), Q9.2 (S), R5.1, R11.1, R17.1, R23.1, R26.2, R29.2, R32.1, R35.2, R36.2, U1.6 (GND), U1.17 (GND), U2.2 (GND), U3.2 (GND), U5.4 (GND), U18.7 (GND), U18.17 (GND); also elsewhere on the board
unnamed: C7.2, R29.1, R30.2
unnamed: C69.2, R50.1
unnamed: D1.2 (A), R27.1
unnamed: D2.2 (A), R41.1
unnamed: Q1.1 (G), R15.2
unnamed: Q1.5 (S), R7.1
unnamed: Q1.3 (G), R14.2
unnamed: Q1.2 (S), R6.1
unnamed: Q2.3 (D), Q3.3 (G), R28.2
unnamed: C68.2, Q4.3 (G), R37.1, R49.2, R50.2
unnamed: C68.1, Q4.4 (S), R31.2, R37.2, U18.15 (RS-)
unnamed: TP6.1, U1.11 (IO6)
unnamed: R18.1, U1.13 (~RESET)
unnamed: C2.1, R19.1, R21.1, U2.1 (INP)
unnamed: R14.1, U2.4 (OUT)
unnamed: C3.1, R20.1, R22.1, U3.1 (INP)
unnamed: R15.1, U3.4 (OUT)
unnamed: R24.2, U5.1 (NO1)
unnamed: R25.2, U5.5 (NO2)
unnamed: R34.1, R36.1, TP14.1, U18.10 (CIN1+)
unnamed: R33.1, R35.1, TP12.1, U18.11 (CIN1-)
unnamed: R33.2, U18.8 (CIN2+), U18.12 (REF)
unnamed: R30.1, U18.5 (INHIBIT)
unnamed: R34.2, U18.14 (IOUT)
unnamed: TP11.1, U18.13 (POUT)
unnamed: Q3.1 (D), Q3.2 (D), Q3.5 (D), Q3.6 (D), R31.1, U18.16 (RS+)
VBUS: Q3.4 (S), R28.1; also elsewhere on the board
VPD-Q1: C4.1, C8.1, C9.1, R1.1, R3.1, R9.1, R13.1, R18.2, R21.2, R22.2, R38.2, TP2.1, U1.14 (V+), U2.5 (VDD), U3.5 (VDD)

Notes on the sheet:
OreSat Power Domain (OPD) Controller
RW Q1 has OPD Address 0x20
ON/~{OFF} signal powers MAX4211 + TS5A Saves quiescent OPD power draw
Circuit breaker switch with ~10 ms soft start
OreSat Power Domain (OPD) Power Supply (3.3V)
> 100 ms low on MAX7310 output will disconnect MAX7310 from OPD I2C.
250 ms inhibit on power up
1206
Card Power Switch and Circuit Breaker
UART switch
Main Power Switch Vbus = (6.0, 7.2, 8.4) V
Allows ~ 4.0 A continuous


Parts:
C18, C21, C24, C26: 100n; 0603-C-NOSILK; MPN C0603C104K5RACAUTO
C22, C23, C25, C27: 1u; 0603-C-NOSILK; MPN GRT188R71E105KE13D
C30: 10n; 0603-C-NOSILK; MPN C0603C103J5RACAUTO
C31: 470n; 0603-C-NOSILK; MPN C0603C474K3RACAUTO
D7: AMBER; LED_0603_1608Metric_Pad1.05x0.95mm_HandSolder; MPN 150060AS75000
D9: GREEN; LED_0603_1608Metric_Pad1.05x0.95mm_HandSolder; MPN 150060GS75000
Q11: DMP2240UDM-7; SOT-23-6; MPN DMP2240UDM-7
Q12, Q15: DMN3028LQ-7; SOT-23; MPN DMN3028LQ-7
Q13, Q14: DMPH2040UVTQ-7; TSOT-23-6; MPN DMPH2040UVTQ-7
R89: 10; 0603-C-NOSILK; MPN RMCF0603FT10R0
R90, R94, R95, R98, R100, R115, R116: 100; 0603-C-NOSILK; MPN RMCF0603FT100R
R91, R92, R93, R96, R97, R99, R101, R104, R105: 100; 0603-C-NOSILK; not fitted
R102, R103: 665k; 0603-C-NOSILK; MPN RMCF0603FT665K
R106, R111, R112, R114, R118, R122, R124, R126, R127, R128, R129, R130, R132: 10k; 0603-C-NOSILK; MPN RMCF0603FT10K0
R107, R108: 330k; 0603-C-NOSILK; MPN RMCF0603FT330K
R109, R110: 1M; 0603-C-NOSILK; MPN RMCF0603FT1M00
R113: 4.7k; 0603-C-NOSILK; MPN RMCF0603FT4K70
R117: 100k; 0603-C-NOSILK; MPN RMCF0603FT100K
R119: 15m; 1206-C; MPN CSNL1206FT15L0
R123: 0; 0603-C-NOSILK; MPN RMCF0603ZT0R00
R125: 0; 0603-C-NOSILK; not fitted
TP38, TP39, TP40, TP41, TP45, TP46, TP47, TP49, TP50, TP51, TP54, TP55: Test-Point; TestPoint-0.75mm-th
U12: MAX7310; QFN-16-1EP_4x4mm_P0.65mm_EP2.1x2.1mm; MPN MAX7310ATE
U13, U14: MIC842LYC5; SOT-353_SC-70-5; MPN MIC842LYC5-TR
U15: TS5A21366DCUR; VSSOP-8_2.3x2mm_P0.5mm; MPN TS5A21366DCUR
U16: MAX4211FETE; QFN-16-1EP_4x4mm_P0.65mm_EP2.1x2.1mm; MPN MAX4211FETE

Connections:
/C3-UART-RX: R115.1; also elsewhere on the board
/C3-UART-TX: R116.1; also elsewhere on the board
/OPD_PWR: R89.2; also elsewhere on the board
/OPD_SCL: R94.2; also elsewhere on the board
/OPD_SDA: R95.2; also elsewhere on the board
/RW Power Domain Q3/AD0: R100.1, R101.2, R104.1, R105.2, U12.1 (AD0)
/RW Power Domain Q3/AD1: R96.1, R97.2, R98.1, R99.2, U12.2 (AD1)
/RW Power Domain Q3/AD2: R90.1, R91.2, R92.1, R93.2, U12.3 (AD2)
/RW Power Domain Q3/BOOTCFG-Q3: U12.10 (IO5); also elsewhere on the board
/RW Power Domain Q3/CB-RESET: R122.2, TP50.1, U12.9 (IO4), U16.9 (CIN2-)
/RW Power Domain Q3/CB_CTRL: Q15.1 (G), R128.1, TP46.1, U16.3 (LE), U16.4 (COUT1), U16.6 (COUT2)
/RW Power Domain Q3/ON/~OFF: C25.1, C26.1, Q12.1 (G), R112.1, R113.2, TP45.1, U12.8 (IO3), U15.8 (Vcc), U16.1 (VCC), U16.2 (IN)
/RW Power Domain Q3/PEN-SCL-FILT: Q11.4 (D), R90.2, R96.2, R100.2, R107.2, TP39.1, U12.15 (SCL)
/RW Power Domain Q3/PEN-SDA-FILT: Q11.6 (D), R92.2, R98.2, R104.2, R108.2, TP40.1, U12.16 (SDA)
/RW Power Domain Q3/RW-UART-RX-Q3: U15.6 (COM2); also elsewhere on the board
/RW Power Domain Q3/RW-UART-TX-Q3: U15.2 (COM1); also elsewhere on the board
/RW Power Domain Q3/UART_EN: R111.2, U12.12 (IO7), U15.3 (IN2), U15.7 (IN1)
/RW Power Domain Q3/VBUSP-Q3: C27.1, C31.1, Q14.1 (D), Q14.2 (D), Q14.5 (D), Q14.6 (D), R132.2, TP55.1; also elsewhere on the board
/RW Power Domain Q3/~FAULT: Q15.3 (D), R130.1, TP54.1, U12.7 (IO2)
GND: C18.2, C21.2, C22.2, C23.2, C24.2, C25.2, C26.2, D7.1 (K), D9.1 (K), Q12.2 (S), Q15.2 (S), R93.1, R99.1, R105.1, R111.1, R112.2, R117.2, R122.1, R125.2, R126.2, U12.6 (GND), U12.17 (GND), U13.2 (GND), U14.2 (GND), U15.4 (GND), U16.7 (GND), U16.17 (GND); also elsewhere on the board
unnamed: C27.2, R117.1, R118.2
unnamed: C31.2, R129.1
unnamed: D7.2 (A), R113.1
unnamed: D9.2 (A), R132.1
unnamed: Q11.1 (G), R103.2
unnamed: Q11.5 (S), R95.1
unnamed: Q11.3 (G), R102.2
unnamed: Q11.2 (S), R94.1
unnamed: Q12.3 (D), Q13.3 (G), R114.2
unnamed: C30.2, Q14.3 (G), R127.1, R128.2, R129.2
unnamed: C30.1, Q14.4 (S), R119.2, R127.2, U16.15 (RS-)
unnamed: TP41.1, U12.11 (IO6)
unnamed: R106.1, U12.13 (~RESET)
unnamed: C22.1, R107.1, R109.1, U13.1 (INP)
unnamed: R102.1, U13.4 (OUT)
unnamed: C23.1, R108.1, R110.1, U14.1 (INP)
unnamed: R103.1, U14.4 (OUT)
unnamed: R115.2, U15.1 (NO1)
unnamed: R116.2, U15.5 (NO2)
unnamed: R124.1, R126.1, TP51.1, U16.10 (CIN1+)
unnamed: R123.1, R125.1, TP49.1, U16.11 (CIN1-)
unnamed: R123.2, U16.8 (CIN2+), U16.12 (REF)
unnamed: R118.1, U16.5 (INHIBIT)
unnamed: R124.2, U16.14 (IOUT)
unnamed: TP47.1, U16.13 (POUT)
unnamed: Q13.1 (D), Q13.2 (D), Q13.5 (D), Q13.6 (D), R119.1, U16.16 (RS+)
VBUS: Q13.4 (S), R114.1; also elsewhere on the board
VPD-Q3: C18.1, C21.1, C24.1, R89.1, R91.1, R97.1, R101.1, R106.2, R109.2, R110.2, R130.2, TP38.1, U12.14 (V+), U13.5 (VDD), U14.5 (VDD)

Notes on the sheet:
Card Power Switch and Circuit Breaker
250 ms inhibit on power up
OreSat Power Domain (OPD) Controller
RW Q3 has OPD Address 0x22
ON/~{OFF} signal powers MAX4211 + TS5A Saves quiescent OPD power draw
Circuit breaker switch with ~10 ms soft start
OreSat Power Domain (OPD) Power Supply (3.3V)
UART switch
> 100 ms low on MAX7310 output will disconnect MAX7310 from OPD I2C.
Main Power Switch Vbus = (6.0, 7.2, 8.4) V
Note: Address 0b0111110x is reserved on all oresat cards
1206
Allows ~ 4.0 A continuous

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

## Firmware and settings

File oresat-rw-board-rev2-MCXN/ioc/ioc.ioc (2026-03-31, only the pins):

Mcu.UserName=STM32G474VEHx
PA0.GPIO_Label=PHA_I
PA0.Signal=ADC1_IN1
PA1.GPIO_Label=PHC_I
PA1.Signal=ADC2_IN2
PA10.GPIO_Label=PHB_H
PA10.Signal=HRTIM1_CHB1
PA11.GPIO_Label=PHB_L
PA11.Signal=HRTIM1_CHB2
PA13.Signal=SYS_JTMS-SWDIO
PA14.Signal=SYS_JTCK-SWCLK
PA15.GPIO_Label=SPI_nCS
PA15.Signal=SPI3_NSS
PA2.GPIO_Label=PHA_V
PA2.Signal=ADC1_IN3
PA4.GPIO_Label=DAC_1
PA4.Signal=COMP_DAC11_group
PA5.GPIO_Label=DAC_2
PA5.Signal=COMP_DAC12_group
PA6.Signal=COMP_DAC21_group
PA7.GPIO_Label=PHC_V
PA7.Signal=ADC2_IN4
PA8.GPIO_Label=PHA_H
PA8.Signal=HRTIM1_CHA1
PA9.GPIO_Label=PHA_L
PA9.Signal=HRTIM1_CHA2
PB1.GPIO_Label=PHB_I
PB1.Signal=ADC3_IN1
PB3.GPIO_Label=SWO
PB3.Signal=GPIO_Output
PB5.GPIO_Label=CAN_ADDR1
PB5.Signal=GPIO_Input
PB7.GPIO_Label=CAN_ADDR0
PB7.Signal=GPIO_Input
PB8-BOOT0.GPIO_Label=BOOT0
PB8-BOOT0.Signal=GPIO_Input
PC10.GPIO_Label=SPI_SCK
PC10.Signal=SPI3_SCK
PC11.GPIO_Label=SPI_MISO
PC11.Signal=SPI3_MISO
PC12.GPIO_Label=SPI_MOSI
PC12.Signal=SPI3_MOSI
PC8.GPIO_Label=PHC_H
PC8.Signal=HRTIM1_CHE1
PC9.GPIO_Label=PHC_L
PC9.Signal=HRTIM1_CHE2
PD0.GPIO_Label=CAN_RX
PD0.Signal=FDCAN1_RX
PD1.GPIO_Label=CAN_TX
PD1.Signal=FDCAN1_TX
PD2.GPIO_Label=DEBUG1
PD2.Signal=GPIO_Output
PD3.GPIO_Label=DEBUG3
PD3.Signal=GPIO_Output
PD4.GPIO_Label=DEBUG0
PD4.Signal=GPIO_Output
PD5.GPIO_Label=DEBUG_TX
PD5.Signal=USART2_TX
PD6.GPIO_Label=DEBUG_RX
PD6.Signal=USART2_RX
PD7.GPIO_Label=DEBUG2
PD7.Signal=GPIO_Output
PE0.GPIO_Label=DFU_TX
PE0.Signal=USART1_TX
PE1.GPIO_Label=DFU_RX
PE1.Signal=USART1_RX
PE10.GPIO_Label=THERM3
PE10.Signal=ADC5_IN14
PE11.GPIO_Label=THERM2
PE11.Signal=ADC5_IN15
PE12.GPIO_Label=THERM0
PE12.Signal=ADC5_IN16
PE14.GPIO_Label=VBUS_V
PE14.Signal=ADC4_IN1
PE2.Signal=SYS_TRACECLK
PE3.Signal=SYS_TRACED0
PE4.Signal=SYS_TRACED1
PE5.Signal=SYS_TRACED2
PE6.Signal=SYS_TRACED3
PE8.GPIO_Label=THERM1
PE8.Signal=ADC5_IN6
PE9.GPIO_Label=PHB_V
PE9.Signal=ADC3_IN2
PF0-OSC_IN.Signal=RCC_OSC_IN
PF1-OSC_OUT.Signal=RCC_OSC_OUT
PG10-NRST.GPIO_Label=nRST
PG10-NRST.Signal=GPIO_Input

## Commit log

2018-02-08 Here is what I have so far for the motor controller. The first page of the schematic is the oresat proto-card. I did not change anything there. The second page is my work.
    [controller.sch]
2018-02-09 I added in the STSPIN250 IC. I chose capacitors and resistors by following directions from its datasheet and refrencing the ST motor shield as well.
    [controller.sch]
2018-02-11 Updated the symbol for the op amp. Updated values of R7 and R8.
    [controller.sch]
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2018-02-14 Max and I started assigning the MCU pinout. We completed PWM pins.
    [controller.sch]
2018-02-15 Updated the symbol of the op amp and reorientated the components so it actually looks like a non-inverting amplifier. I also started assigning the GPIO pins. I am using a HEX SPDT switch to switch th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
    [controller.sch]
2018-02-17 Reconfigured pinout. Biased the voltage of the REF pin to 0.5V on the STSPIN250 IC.
    [controller.sch]
2018-02-18 Added the encoder to the schematic. We need to configure the F0 to have a SPI chip select pin to connect to the CSn pin on the encoder.
    [controller.sch]
2018-02-21 Removed unneeded text and did some cleanup. Everything looks good except the encoder has a CSn pin that needs to connect to the F0 MCU somehow. The CSn pin is for SPI chip select. Where do we connect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
    [controller.sch]
2018-02-21 Ran ERC, fixed some things and approved some things.
    [controller.sch]
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2018-02-21 Design review with Nathan. Lots of little changes, mostly cosmetic. Moved from Protocard to smaller ACS board by removing protocard junk.
    [controller.sch]
2018-02-22 Cosmetic fixes: Added labels. All resistors and capacitors are numbered. Updated the symbol of the encoder. Updated the symbol and package of the STSPIN230. Boxed LEDs and placed a note "NP FOR FLIGH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
    [controller.sch]
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2018-02-24 Nice job, Nathan! Did a bit of visual polish, updated AMS symbol to be more compact. Big changes: Added new TPS63070 SPS circuit from solar board, redid LEDs on magnetorquer. BLDC LEDs should be that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
    [controller.sch]
2018-02-24 Removed EPAD from both motor driver package footprints and updated the part in the schematic.
    [broken.brd, controller.sch]
2018-02-24 Checked all ERC. Looks good. Eric go ahead and start board layout again.
    [controller.sch]
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2018-03-02 add Q-out/ more on layout
    Quadrature output has been added to the schematic for Josh to collect data from motor spec test.
    [controller.brd, controller.sch]
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2018-03-11 boards to send off
    Tried clearing up the ground plane. Everything I tried just made it worse.
    [controller.brd, controller.sch]
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2018-03-17 Board revisions
    Started redesign of compacted layout, and flat layout for system testing.
    [PRO_controller.brd, PRO_controller.sch, broken.brd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]
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2018-05-21 Clean up from last week: added three test points because test points are important when you might need a signal, and added signal names because N names are dumb, and cleaned up a few ERC warnings. An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
    [controller_rev3.brd, controller_rev3.sch]
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2018-06-05 The frame said Rev 1.1. I fixed that to say Rev 3.
    [controller_rev3.sch]
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2019-07-16 Current set of modifications for Rev4.1 completed, some errors found and corrected
    [controller_rev4(b).csv, controller_rev4.1.brd, controller_rev4.1.sch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]
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2020-01-27 Flex cable prototype
    [connector_cable.brd, connector_cable.sch, controller_rev4.2b.brd]
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2020-01-27 connector corrections
    [powerDomaine_rev3.4.brd]
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2020-01-29 Rename the card file, and it doesn't need a vesion number (that's what git is for)
    [oresat-acs-card.brd, oresat-acs-card.sch]
2020-01-29 Sanity check Eric's card. Removing supply symbols even though this is causing Andrew physical pain but EAGLE can't deal with renaming supply symbols. Also more text.
    [oresat-acs-card.brd, oresat-acs-card.sch]
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2020-06-26 Layed out power domains for four quadrants, added another power domain and an STM32F042. Also added breaker circuit and I2C buffer for Magnetometers, and an IMU
    [oresat-acs-card.brd, oresat-acs-card.sch]
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2020-07-02 Reworked board layout to avoid space taken up by inhibit switches on battery board
    [oresat-acs-card.brd]
2020-07-05 Added 10k pull down resistors to SDO pins on IMU. Added labels to magnetometer breaker and value for current set resistor. Removed unused nets connected to the MCU.
    [oresat-acs-card.brd, oresat-acs-card.sch]
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2020-07-20 Floated BMI088 CSB2 because CSB1 was and data sheet said it had a pull up; switched to card outline with no RF connectors (whoops), moved ground stitching near edges to under TSTOP, fixed some DRC er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
    [oresat-acs-card.brd, oresat-acs-card.sch]
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2020-09-08 Doubled up MAG_SDA and MAG_SCL on backplane connector to match backplane, and added pull up resistors for these signals. Updated BOM to reflect this.
    [oresat-acs-card-bom.xlsx, oresat-acs-card.brd, oresat-acs-card.sch]
2020-09-11 Moved some things around to make space to add mounting holes for the magnetorquers!
    [oresat-acs-card.brd]
2020-09-21 Standardized passives to 0603 and changed all test points to circular footprint. Spaced out components in OPD for easier stuffing. Cleaned up names layer. Fixed OPD protection circuit to match OPD de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
    [oresat-acs-card.brd, oresat-acs-card.sch]
2020-09-21 Doubled up spare lines on back connector and added some ground vias.
    [oresat-acs-card.brd, oresat-acs-card.sch]
2020-09-22 Fixed attributes and updated BOM. Also doubled up backplane connector lines and added some test points.
    [oresat-acs-card-bom.xlsx, oresat-acs-card.brd, oresat-acs-card.sch]
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2020-11-24 Updated ACS card to card outline v1.3, and removed old corner holes
    [oresat-acs-card.brd, oresat-acs-card.sch]
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2021-04-08 Updated board version, added fiducials, added OPD inrush circuit values, added TPs on I2C lines.
    [oresat-acs-card.brd, oresat-acs-card.sch]
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2022-02-07 Fixed ERC/DRC errors and design rules
    [rev6.0_flat_controlstage.kicad_pcb, rev6.0_flat_controlstage.kicad_sch]
2022-02-08 Fix DRC issues on power stage
    [rev6.0_flat_powerstage.kicad_sch]
2022-02-09 Updated .gitignore file with KiCAD files; removed a bunch of committed temp files.
    [rev6.0_flat_controlstage_bak.kicad_sch]
2022-02-09 Added BoM, fixed footprints
    [rev6.0_flat_controlstage.csv, rev6.0_flat_powerstage.csv, rev6.0_flat_powerstage.kicad_sch]
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2022-04-03 Added magnetorquer circuitry to ACS card. Updated backplane to 2.0. Moved ACS card to kicad.
    [Connectors.kicad_sch, Magnetorquers.kicad_sch, Microcontroller.kicad_sch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]
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2022-05-29 Updated ACS board. Changed mezzanine pinouts. Added 5 V supplies for each quadrant. Updated layout.
    [Connectors.kicad_sch, Q1_Power_Domain.kicad_sch, Q2_Power_Domain.kicad_sch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]
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2022-07-08 Updated 5 V regulator and tweaked card layout. Cleaned up silkscreen layer and schematic.
    [Connectors.kicad_sch, Download_STP_691243100006 (rev1).stp, Magnetorquers.kicad_sch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]
2022-07-12 Updated 5V regulators to match design block. Added UART switch to microcontroller. Added power flags and cleaned up ERC errors
    [Connectors.kicad_sch, Magnetorquers.kicad_sch, Microcontroller.kicad_sch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]
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2022-07-19 Beginning cleanup of the ADCS repo. Removing kicad and eaglecad and trying to make sense of all of this.
    [Download_STP_691243100006 (rev1).stp, oresat-acs-card-sch-connectors.kicad_sch, oresat-acs-card-sch-magnetorquers.kicad_sch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]
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2022-07-19 Give rev6 and rev7 common names, and update the license to CERN OHL v2.
    [10132797-021100LF.stp, 10132798-021100LF.stp, 555600307.stp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]
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2023-01-15 Added ADCS card mezzanine flex pcb
    [mezzanine-flex-board.kicad_pcb, mezzanine-flex-board.kicad_sch]
2023-01-15 Extended mezzanine flex pcb so that we can slide the connector, and added silkscreen name
    [mezzanine-flex-board.kicad_pcb]
2023-01-16 Cleaned up comments on flex pcb
    [mezzanine-flex-board.kicad_pcb]
2023-02-13 Fixed ADCS card issues
    [oresat-adcs-card-sch-magnetorquers.kicad_sch, oresat-adcs-card-sch-microcontroller.kicad_sch, oresat-adcs-card-sch-q1-power.kicad_sch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]
2023-02-20 Fixed more ADCS card issues
    [oresat-adcs-card-sch-magnetorquers.kicad_sch, oresat-adcs-card-sch-q1-power.kicad_sch, oresat-adcs-card-sch-q2-power.kicad_sch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]
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2023-06-07 Fix clearances, fix silk, add vias
    [control-stage.kicad_pcb]
2023-06-09 Add shorter caps under reaction wheel, update thermal jumpers, add addl. debug test points to control board, silk pass
    [CKG57N.step, arm.stp, control-stage.kicad_pcb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]
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2023-07-20 Updated ADCS card and fixed library issues
    [oresat-adcs-card-sch-connectors.kicad_sch, oresat-adcs-card-sch-magnetorquers.kicad_sch, oresat-adcs-card-sch-microcontroller.kicad_sch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]
2023-10-24 rev 7.1 before MA702 swap
    [control-stage.kicad_pcb]
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2024-02-25 changed mezanine flex board to shorten to 14.5mm down from 19mm
    [mezzanine-flex-board.kicad_pcb, mezzanine-flex-board.kicad_sch]
2024-02-25 mezanine flex PCB changed to pours on back instead of straight traces
    [mezzanine-flex-board.kicad_pcb]
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2024-02-26 Updated RW mezzanine breakout to be 2 sided osh park PCB with silk and everything. Made shorter to try and fit with ADCS card below the RW board, and avoid RW board fasteners.
    [mezzanine-breakout-board.kicad_pcb]
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2024-05-06 Added worksheet variables, Made OPD resistors NP appropriately, revamped the BOM table, and started working on fixing the BOM table and all the values that we seem to have lost?!
    [oresat-adcs-card-sch-card-power.kicad_sch, oresat-adcs-card-sch-connectors.kicad_sch, oresat-adcs-card-sch-magnetorquers.kicad_sch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]
2024-05-19 Fixed missing component values
    [oresat-adcs-card-sch-card-power.kicad_sch, oresat-adcs-card-sch-magnetorquers.kicad_sch, oresat-adcs-card-sch-microcontroller.kicad_sch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]
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2025-11-24 Small fixes on pre-fabbed board
    Fixed Sch to PCB sync, updated footprints to library, OK'd DRCs, messed with 3.3VD SPS.
    [control-stage.kicad_pcb]
2025-11-24 Updated schematic symbols
    Updated schematic symbols to have yellow background and fixed a couple of local net labels
    [oresat-mag-card-sch-magnetorquers.kicad_sch, oresat-mag-card-sch-microcontroller.kicad_sch, oresat-mag-card-sch-power.kicad_sch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]
2025-11-24 Fixed 5V routing around 3.3v SMPS, added board silkscreen
    [control-stage.kicad_pcb]
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2025-12-15 Schematic review with some small fixes
    [oresat-mag-card-sch-microcontroller.kicad_sch, oresat-mag-card-sch-power.kicad_sch, oresat-mag-card-sch-sensors.kicad_sch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]
2025-12-16 Schematic Update
    Updated schematic to fix all ERC violations and errors, removed all traces of old EAGLE imported components and replaced with either OreSat or Kicad native symbols and footprints.
    [oresat-mag-card-sch-magnetorquers.kicad_sch, oresat-mag-card-sch-microcontroller.kicad_sch, oresat-mag-card-sch-power.kicad_sch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]
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2025-12-19 Design review changes on schematic.
    Fixed UART lines, relabeled some OPD outputs from the MAX7310, fixed I2C pullups, lots of small polishing. Ready for layout.
    [oresat-mag-card-sch-magnetorquers.kicad_sch, oresat-mag-card-sch-microcontroller.kicad_sch, oresat-mag-card-sch-power.kicad_sch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]
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2026-01-07 Schematic Done + Board outline set
    Fixed heirarchical labels, cleaned up ERCs, board is ready for layout
    [oresat-rw-card-sch-q1.kicad_sch, oresat-rw-card-sch-q2.kicad_sch, oresat-rw-card-sch-q3.kicad_sch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]
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2026-03-04 Commit because I was told to
    Also fixed a lot of things
    [oresat-rw-card-sch-q1.kicad_sch, oresat-rw-card-sch-q2.kicad_sch, oresat-rw-card-sch-q3.kicad_sch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]
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2026-03-08 No DRC errors
    [oresat-rw-card.kicad_pcb]
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2026-03-10 Fixed a few small BOM issues, checked everything, ready for fab.
    [oresat-rw-card-sch-q1.kicad_sch, oresat-rw-card-sch-q2.kicad_sch, oresat-rw-card-sch-q3.kicad_sch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]
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2026-03-13 Final Push
    Updated I2C buffer because SCL and SDA were swapped, added copper backfill to layer 3. Added extra caps to u3 and u2.
    [oresat-mag-card-sch-sensors.kicad_sch, oresat-mag-card.kicad_pcb]
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2026-04-02 Schematic polish, fixed UART TX/RX mixup, imported into layout
    [oresat-mag-card-sch-magnetorquers.kicad_sch, oresat-mag-card-sch-microcontroller.kicad_sch, oresat-mag-card-sch-power.kicad_sch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]
2026-04-03 Fixed Footprint/Symbol Library Issue
    [power-stage-rev8.kicad_pcb]
2026-04-03 mcxn V2 boards good for fab (aside from invincible silkscreen glitch???)
    [10132797-021100LF.stp, 10132797-031100LF.stp, 10132798-021100LF.stp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]
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2026-04-06 Fix BOM - some packages were wrong size, caught by CM.
    [oresat-rw-card-sch-q1.kicad_sch, oresat-rw-card-sch-q2.kicad_sch, oresat-rw-card-sch-q3.kicad_sch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]
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2026-04-20 Updated keepout on MCXN RW board mezzanine connector and fixed kicad .gitignore for kicad 10
    [power-stage-rev8.kicad_pcb]
2026-04-20 RW Flex board for Mezzanine connectors v1.2
    This board is for RW board v8.0 and RW card v1.0. Note specialized Makefile for flex board including stiffeners.
    [mezzanine-flex-board.kicad_pcb, mezzanine-flex-board.kicad_sch]
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2026-06-30 Cleaned up RW flex to v1.3
    This version upgrade makes the flex board a bit smaller now that we know that the length works and gets rid of the solder mask weirdness from previous versions.
    Cleaned up the README file in order to get another vendor to make the board.
    [mezzanine-flex-board.kicad_pcb]

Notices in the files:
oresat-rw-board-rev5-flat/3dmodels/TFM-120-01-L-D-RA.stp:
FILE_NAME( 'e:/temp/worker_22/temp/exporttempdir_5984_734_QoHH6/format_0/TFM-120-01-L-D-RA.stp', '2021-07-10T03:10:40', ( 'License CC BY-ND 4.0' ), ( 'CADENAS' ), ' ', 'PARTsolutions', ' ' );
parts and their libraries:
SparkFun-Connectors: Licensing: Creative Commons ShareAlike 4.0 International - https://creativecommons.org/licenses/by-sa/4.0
